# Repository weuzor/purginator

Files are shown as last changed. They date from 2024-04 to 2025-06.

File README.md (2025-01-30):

# The Purginator - a purge bucket for the Voron2

The purginator, extractor and depressor are modifications for Voron 2 Printers fitted with Voron Tap, umbilical Stealthburner with E3D Revo hotend (other hotends probably work as well), Filametrix Cutter Mod and Enraged Rabbit Carrot Feeder using sensorless homing and running Happy Hare.
In combination they enable multi material printing without purge tower.

## Purginator

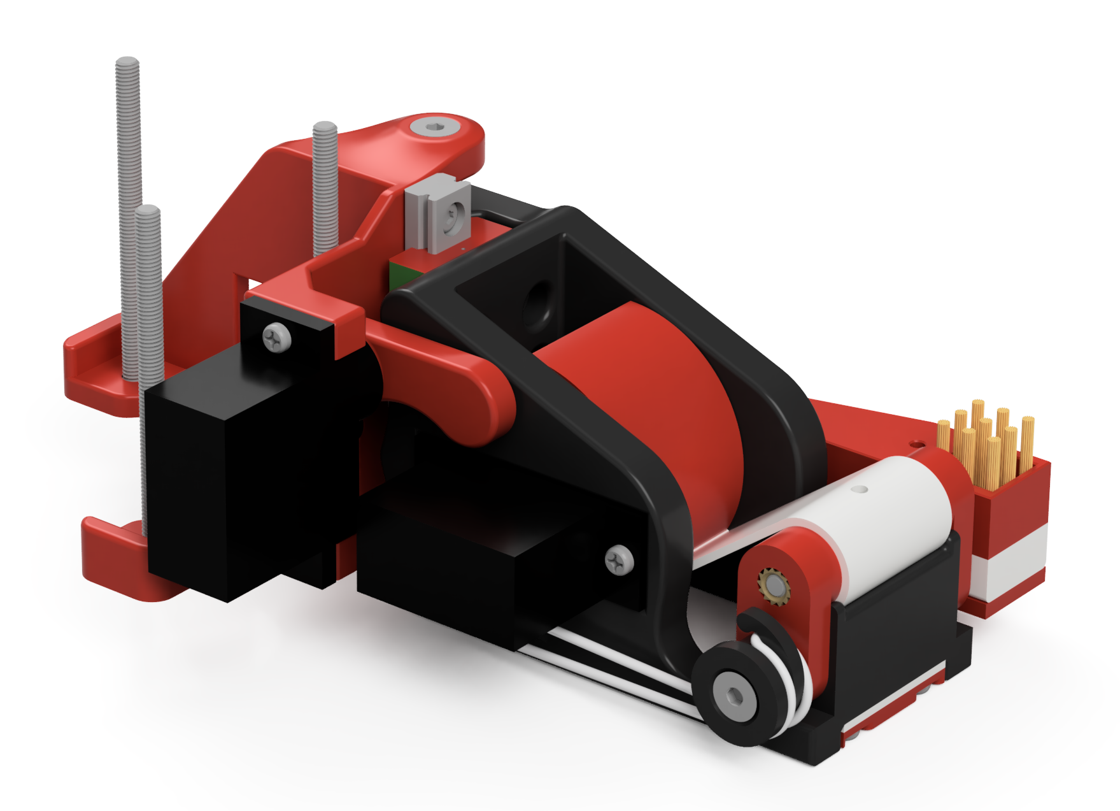
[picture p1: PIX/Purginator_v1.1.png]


([15 min Testprint showing toolchanges and after print nozzle treatment with the purginator](https://youtu.be/EkpkXMRFAnM)). 

## Extractor

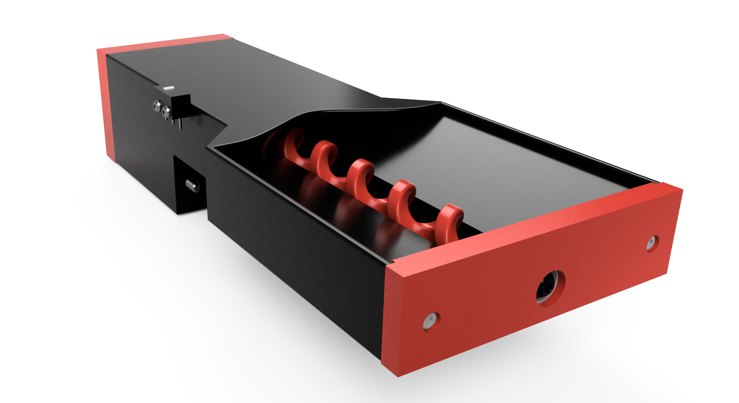
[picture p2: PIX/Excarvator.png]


The extractor is a collecting tray for the purged filament dropped by the purginator.
It has a built in screw conveyor which drags the purged material out of the printer through a small heat trap.
The screw conveyor is powered by a MG90S 360deg Servo.
Once outside the material can either be collected in a suitable container at the back of the printer or if the printer is placed at the rear of a table directly droped into a waste basket on the floor.
This modification requires a cutout in the backpanel. It also restricts z movement to 4 mm below print surface. 
For normal operation this is irrelevant, however if a Z-Homing or Quad Gantry Levelling is performed and the rear left gantry corner is lower than the others by more than 4 mm (e. g. after motors were off and the gantry was moved by whatever cause) the purginator mount would collide with the excarvator. 
To prevent this the extractor has mounting holes for a safety microswitch to trigger an emergency shutdown in this case.

## [Filametrix](https://github.com/sorted01/Filametrix) Depressor 
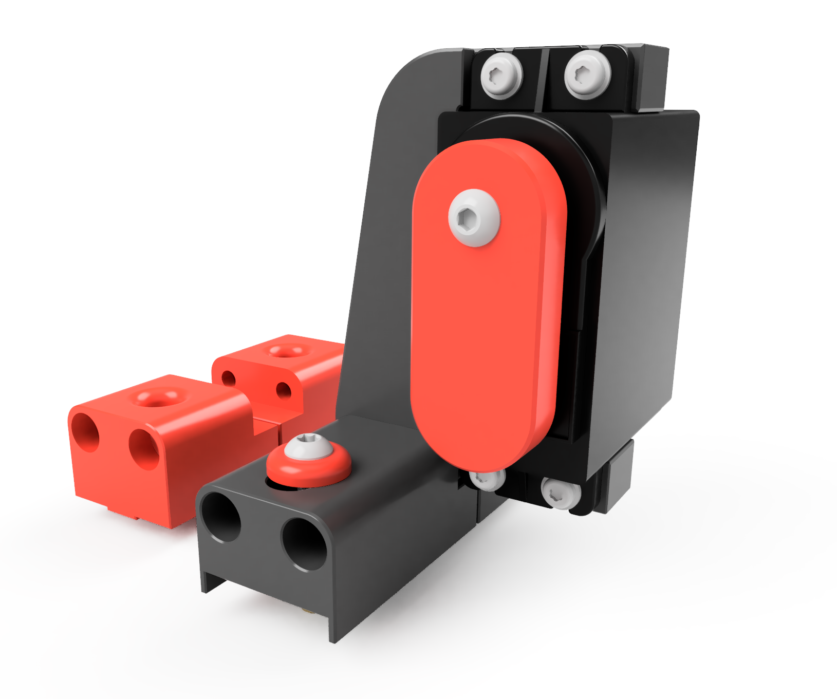
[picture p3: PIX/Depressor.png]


https://github.com/user-attachments/assets/b3596728-9525-4a37-93d0-bf73759ecd00

This mod places a strong enough MG996R Servo at a location where it does not interfere with the toolhead but can depress the filametrix cutter lever with its servo arm.
Thereby the toolhead can remain docked to the purginator during the cutting sequence which eliminates oozing.
Comes with two mounting options for gantries with backers or without.

As an alternative to the gantry mounted depressor this [bowden actuated filament cutter](https://github.com/weuzor/bowden_cutter) can also be used instead to cut any time anywhere :-)

hot1
ex2

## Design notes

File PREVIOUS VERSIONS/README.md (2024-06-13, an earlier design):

# Voron 2 Modifications for multi material printing with ERCF and Stealthburner with Filametrix Cutter
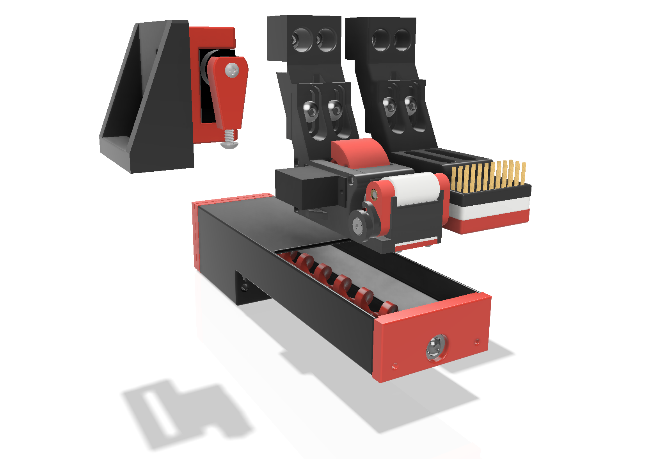
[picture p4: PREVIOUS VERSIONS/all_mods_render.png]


## The Purginator
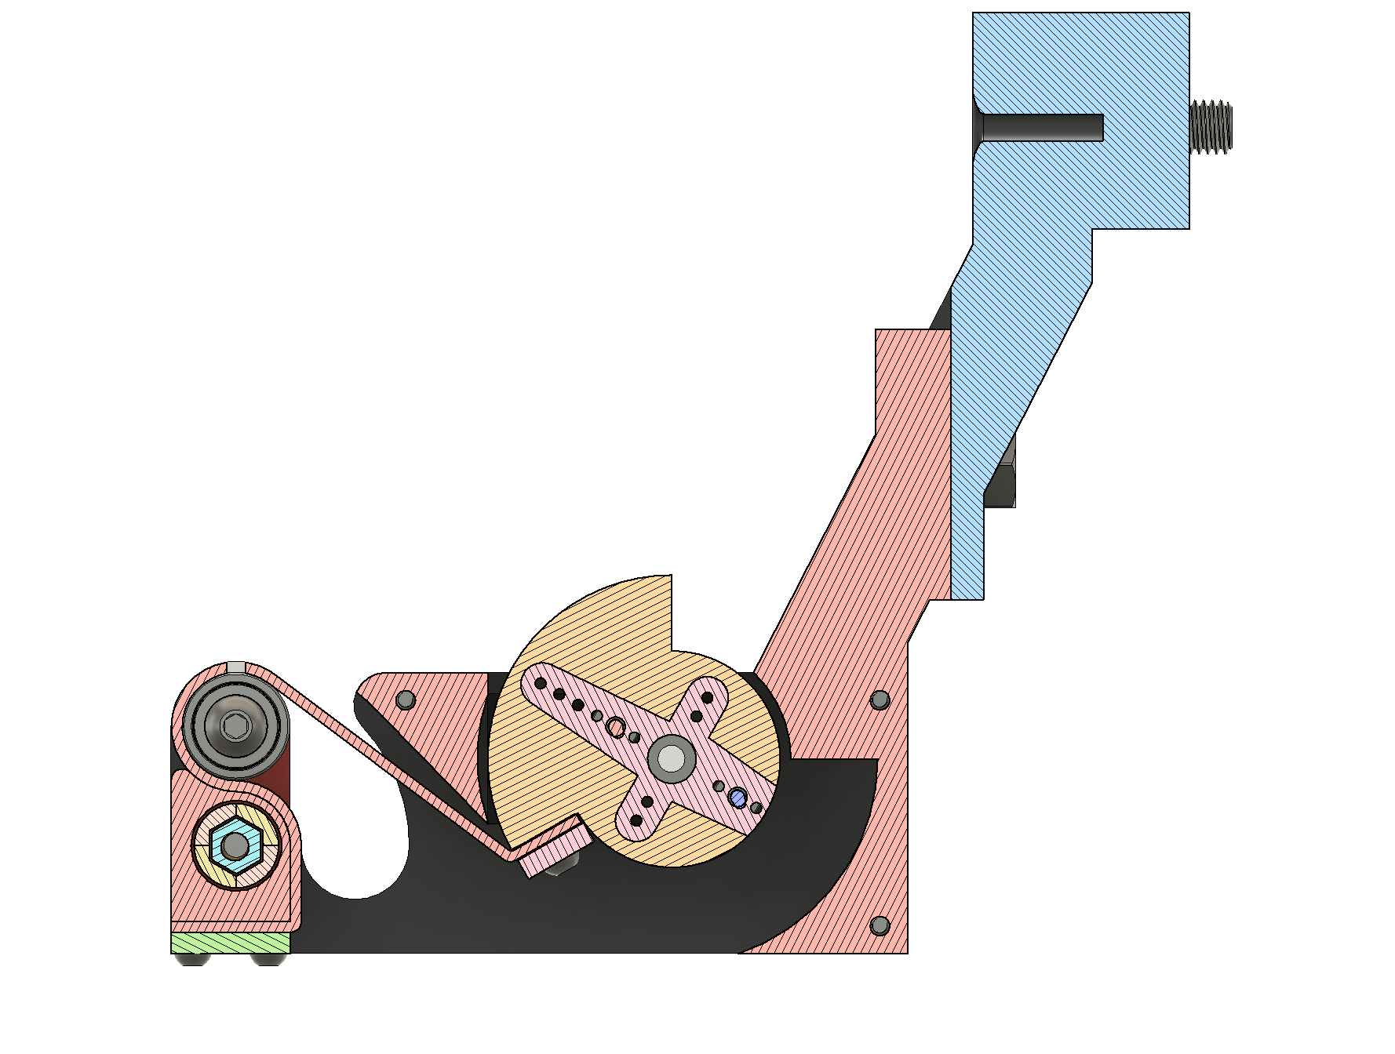
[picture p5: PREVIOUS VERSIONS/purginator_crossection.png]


The purginator is a gantry mounted mechanized purge bucket driven by a MG90S Servo.
In extended position a strip of silicone with a hole is bent into a loop like shape nestling the hole to the nozzle for purging. 
When retracting the silicone strip gets stretched out. This motion wipes the nozzle tip and drops the purged filament.
Installing a purginator enables multi material printing without purge/prime tower thus keeping the entire printbed available for model files. 
[Watch a proof of concept video of a short 3 colour testprint with the purginator, brushinator and gantry servo mount](https://youtu.be/IaCVgWm7dVc). 
It also provides a place to park the toolhead for warmup/cooldown where oozing is no problem.

## The Excarvator
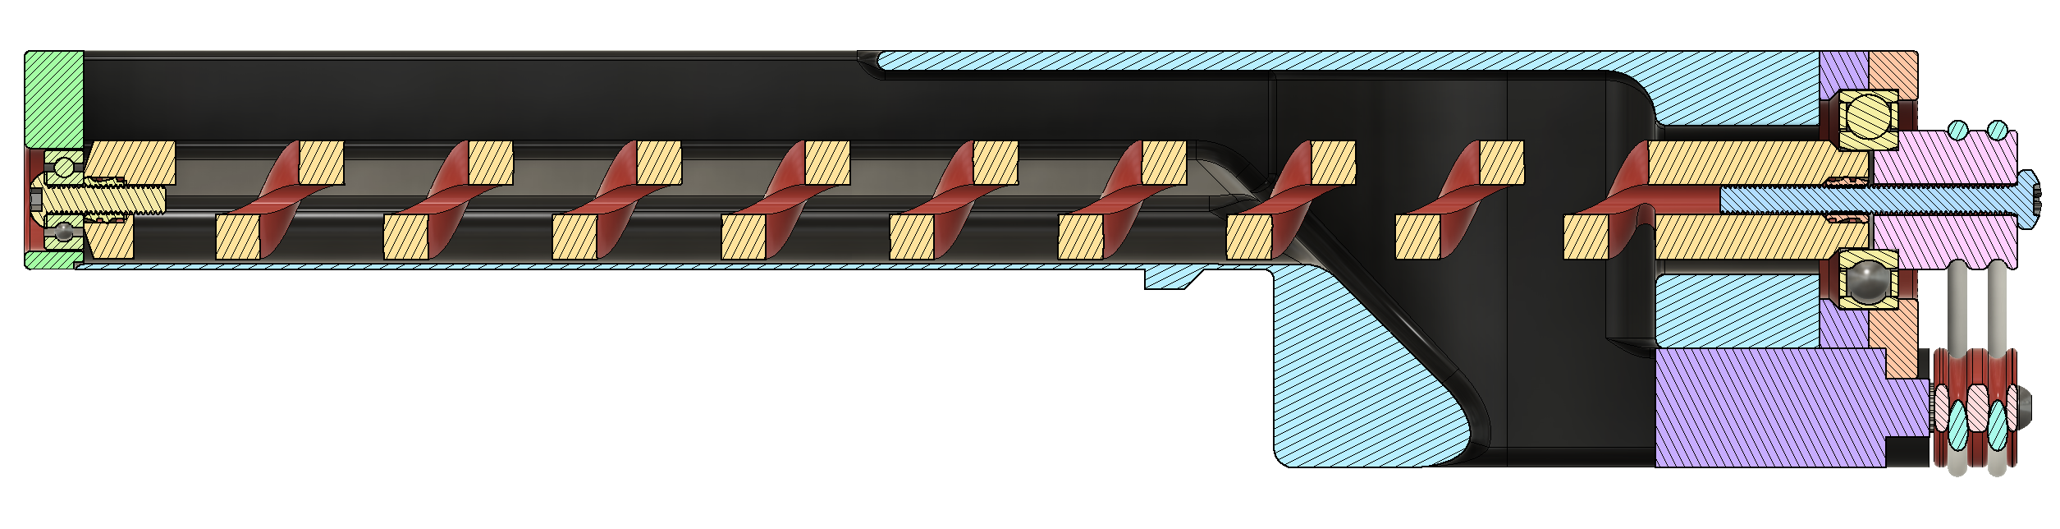
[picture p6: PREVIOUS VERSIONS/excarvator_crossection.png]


The excarvator is a collecting tray for the purged filament dropped by the purginator. It has a built in screw conveyor which drags the purged material out of the printer through a small heat trap.
The screw conveyor is powered by a MG90S 360deg Servo.
Once outside the material can either be collected in a suitable container at the back of the printer or if the printer is placed at the rear of a table directly droped into a waste basket on the floor.
This modification requires a cutout in the backpanel!

## The Brushinator
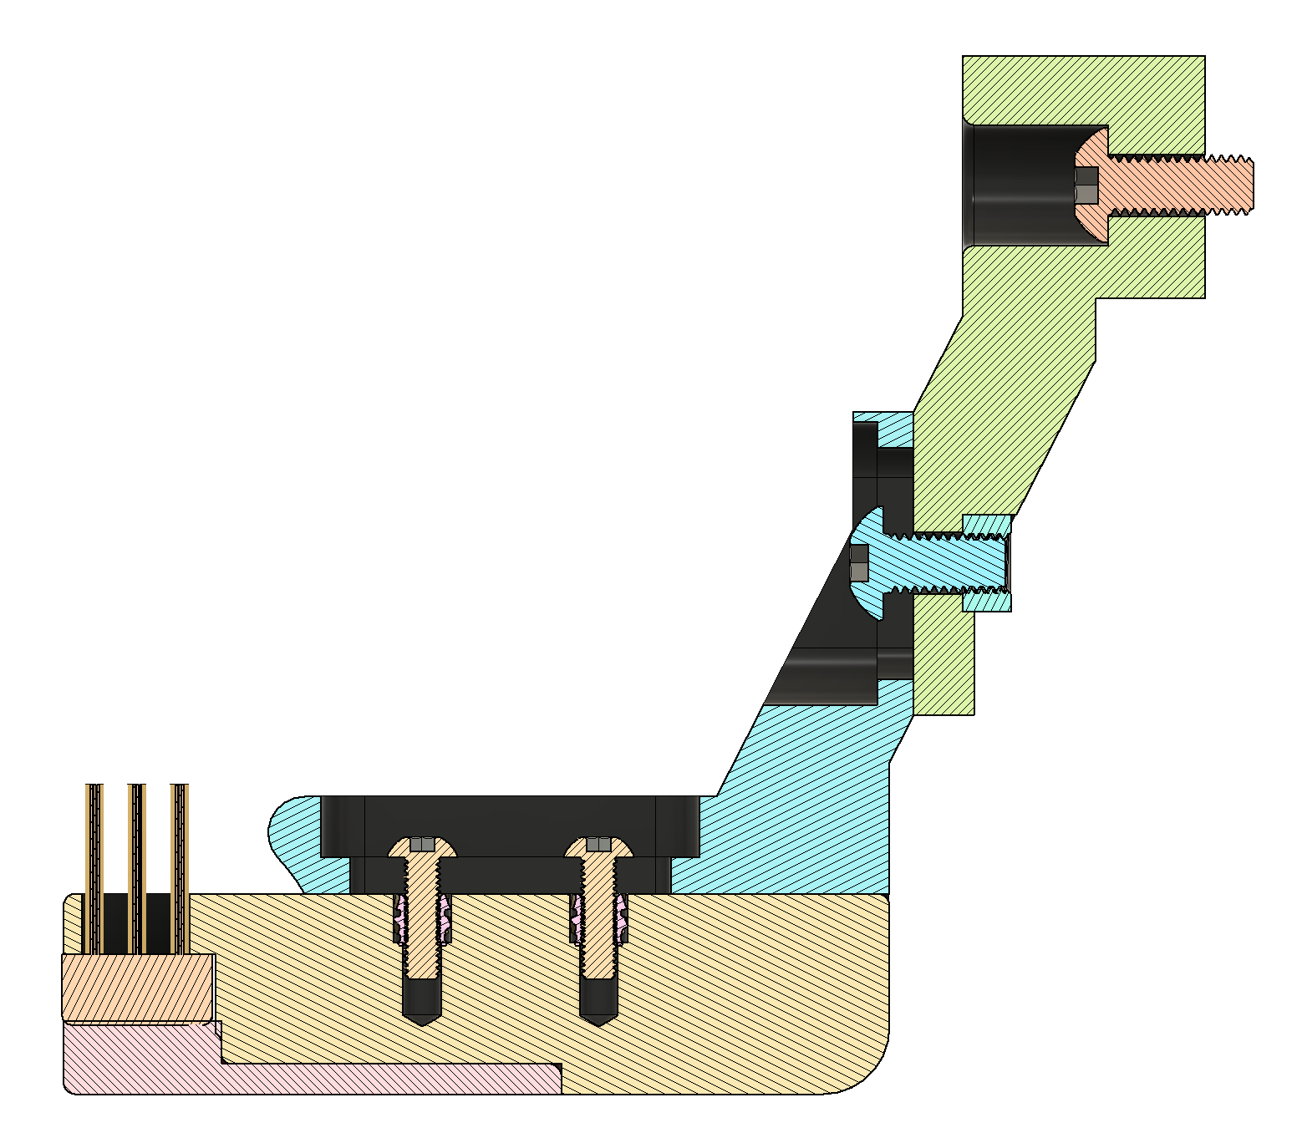
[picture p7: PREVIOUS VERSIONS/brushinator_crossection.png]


The brushinator is a cheap copy of [this gantry mounted nozzle cleaner](https://www.printables.com/de/model/269412-voron-v24-300-gantry-mounted-nozzle-cleaner) matching the purginator design.

## Gantry Servo Mount + Pin
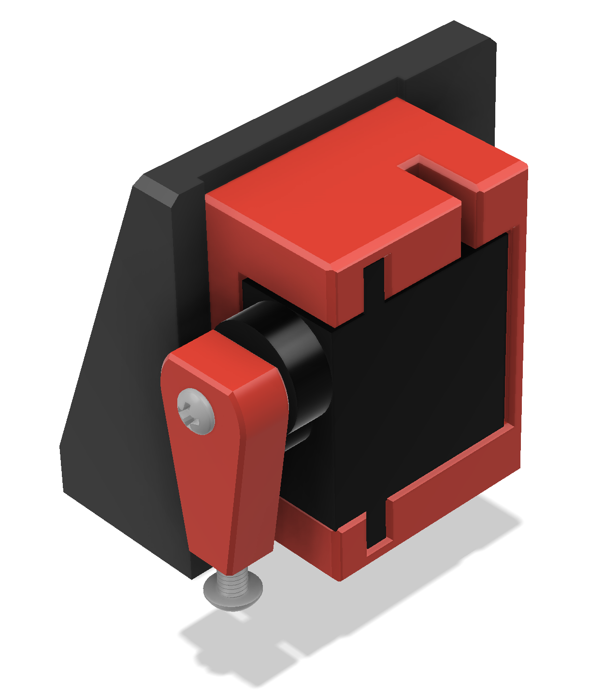
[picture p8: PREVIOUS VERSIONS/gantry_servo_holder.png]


After installing the Filametrix Cutting Mod I realized that the fixed pin interferes with the Stealthburner when moving around the top left corner of the printbed which is something I could not live with.
Since there is a config option for a retracting [Filametrix Cutting Mod](https://github.com/sorted01/Filametrix) pin in the [Happy Hare Software](https://github.com/moggieuk/Happy-Hare) I began my search for the appropriate STL files.
A few hours later I gave up and built my own. It is adjustable in all axes and fits the gantry with or without backers.

## Bill of Materials:

### Purginator 
* [1mm high temperature silicone sheet](https://www.amazon.de/gp/product/B08KFTPTG9/ref=ppx_yo_dt_b_asin_title_o04_s00?ie=UTF8&th=1)
* [1 ea silicone O-Ring 10x14x2mm](https://www.amazon.de/gp/product/B07NQD6KCJ/ref=ppx_yo_dt_b_asin_title_o03_s00?ie=UTF8&th=1)
* [1ea MG90s 180deg Servo](https://www.amazon.de/gp/product/B086V3VP72/ref=ppx_yo_dt_b_asin_title_o00_s00?ie=UTF8&th=1)
* [2ea Ballbearings 3x10x4mm](https://www.amazon.de/stücke-623-2RS-Kugellager-Doppel-Rillenkugellager/dp/B07CWLGNJ5/ref=sr_1_1_sspa?dib=eyJ2IjoiMSJ9.9woqqwQjTq-p6iPwrUffi2d2bsHJw6UycUsB92_u3q-Smt9jMfxYufze3yMLa8dVCcguvt3fg-eWgwVzRmbCx6OBDLn50Iqe8E2cVwwDzqe9K4E6B9IgL00jBknB56GO1ZkXVQhbH0jbnrGV-QxXVfFCnwxjZPuh-A0WkN2nheVrjfzndKp1NyEEW4B8PbHB0m_gXTPkrTWZJLG8WaGOHKBgCCyeGjlpAJjDO7ynSQw.av6AitDux3gb7yG6LLjvQHgYDzAzVkIL2xda3fSPe5c&dib_tag=se&keywords=Kugellager+3x10x4&qid=1710786944&sr=8-1-spons&sp_csd=d2lkZ2V0TmFtZT1zcF9hdGY&psc=1)
* 2ea brass heat insert 4mm
* 2ea M3x10 button head screw
* [1ea 20mm M3 brass standoff](https://www.amazon.de/AMZANDY-NEW-Abstandshalter-Abstandsbolzen-Motherboard-120/dp/B0825XY6VD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)
* 1ea M3x10 countersunk screw
* 1ea M3x20 countersunk screw
* 2ea M2x10 button head screw
* 4ea M2x5 button head screw
* 3ea 2x10 self tapping screw
* 2ea M5x10 button head screw
* 2ea M5 hex nut
* 2ea M5x12 screw
* 2ea M5 roll in T-nuts

### Brushinator 
* 1ea [Brush](https://www.amazon.de/Reinigung-Drahtbürste-Kunststoffgriffe-Edelstahl-Reinigungswerkzeug/dp/B0895GCSH7/ref=sxts_b2b_sx_reorder_acb_customer?content-id=amzn1.sym.f4e69c76-7f1e-4be9-a990-6de7d07aaf6a%3Aamzn1.sym.f4e69c76-7f1e-4be9-a990-6de7d07aaf6a&crid=20N7CF5QOWQE5&cv_ct_cx=messingbürste&dib=eyJ2IjoiMSJ9.z7TWS4HkcxDzHbvJIgCPzA.Y7QLxHE9fQSL7NgeJQ0xp0zurahyunnSiQJpj-z_JAI&dib_tag=se&keywords=messingbürste&pd_rd_i=B0895GCSH7&pd_rd_r=83d5e4a9-06be-4864-90a7-eb933d223a5d&pd_rd_w=HD1Tp&pd_rd_wg=Qrf1B&pf_rd_p=f4e69c76-7f1e-4be9-a990-6de7d07aaf6a&pf_rd_r=70E8QH3QH7KNRC2K66PZ&qid=1710793370&sbo=RZvfv%2F%2FHxDF%2BO5021pAnSA%3D%3D&sprefix=messingbürste%2Caps%2C100&sr=1-1-c8a51df4-6015-4603-b82a-8c2c24cf7e97&th=1)
* 4ea brass heat insert 4mm
* 4ea M3x10 button head screw
* 2ea M5x10 button head screw
* 2ea M5 hex nut
* 2ea M5x12 button head screw
* 2ea M5 roll in T-nuts

### Excarvator
* 1ea M3x30 button head screw
* [2 ea silicone O-Ring 10x14x2mm](https://www.amazon.de/gp/product/B07NQD6KCJ/ref=ppx_yo_dt_b_asin_title_o03_s00?ie=UTF8&th=1)
* 1ea MG90s 360deg Servo (Aliexpress)
* 2ea brass heat insert 4mm
* 1ea M3x10 button head screw
* 1ea ballbearing 3x10x4mm
* 1ea ballbearing 10x22x6mm
* 2ea 2x10 self tapping screw
* 2ea M2.5x16 button head screw
* 2ea M3x16 button head screw

### Gantry Servo Mount & Pin for Filametrix Filament Cutter.
* 1ea 15mm M3 brass standoff
* 1ea M3x16 button head screw
* 1ea MG90s 180deg Servo
* 1ea brass heat insert 4mm
* 1ea M3x10 button head screw

## Building Instructions
### Purginator
* With a ruler and a scalpel cut out a 82x20 mm strip of 1mm thick silicone sheet and punch 2.5 mm holes according to the template. This ist best done with [punch pliers](https://www.amazon.de/AmazonBasics-Leder-Lochzangen-Set-Drehlochzange-verschiedene-Aufweitwerkzeug/dp/B07W48YG15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) and the jig which can be found amongst the stl files.
* Mount the 4 armed servo horn that came with the MG90s servo to the retraction drum using the screws which were included as well and cut the protruding arm flush
* Insert a heat insert in each of the bearing levers
* Mount the ballbearings to the bearing levers
* Fix the 20mm brass standoff to one of the bearing levers using a M3x10 countersunk screw.
* Insert into the main body and the lid
* Mount the second bearing lever and the torque inducer using a M3x20 countersunk screw. Tighten so that the torque inducer does not slip.
* Stretch the silicone O-ring over the torque inducer and fix it to the hook on the main body.
* Mount the silicone strip to the retraction drum using the drum clamp and two M2x10 screws. Make sure the strip is perpendicular to the drum.
* Place the drum in the main body and run the silicone strip in a loop around the bearings.
* Slide the cover in place and secure with three 2x10mm tapping screws.
* Fix the silicone strip end to the housing bottom using the fwd clamp and 4 M2x5 screws. Make sure not to overtighten.
* Check for smooth action.
* Place the M5 hex nuts in the gantry mount (and maybe secure them with some glue)
* Mount the assembly to the gantry mount using two M5x10 button head screws
* The servo should be inserted in position ANGLE=180 and the purginator drum in fully retracted position.
* Mount to the left gantry corner flush to the aluminium extrusion.

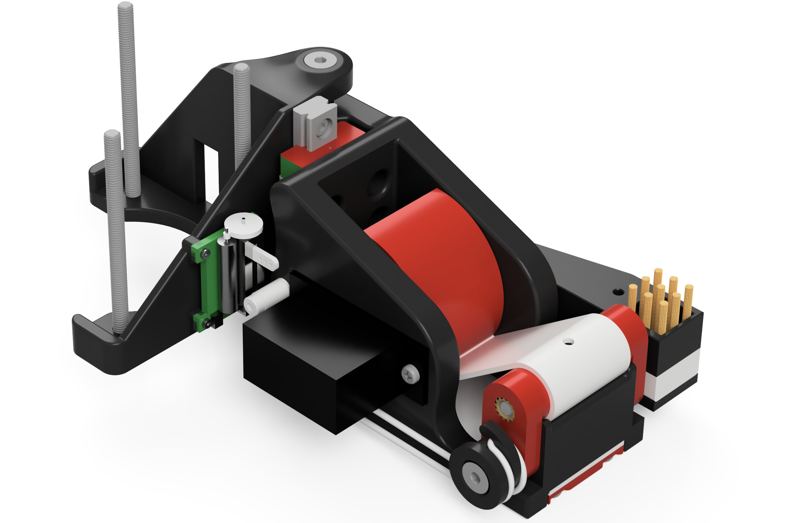
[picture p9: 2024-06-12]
PIX/Purginator_v1.0.png

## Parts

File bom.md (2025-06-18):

# BOM (unfinished work in progress)
## purginator
* 2 [MG90s 180deg servo](https://www.amazon.de/gp/product/B086V3VP72/ref=ppx_yo_dt_b_asin_title_o00_s00?ie=UTF8&th=1)
* 2 [Ballbearing 3x10x4mm](https://www.amazon.de/stücke-623-2RS-Kugellager-Doppel-Rillenkugellager/dp/B07CWLGNJ5/ref=sr_1_1_sspa?dib=eyJ2IjoiMSJ9.9woqqwQjTq-p6iPwrUffi2d2bsHJw6UycUsB92_u3q-Smt9jMfxYufze3yMLa8dVCcguvt3fg-eWgwVzRmbCx6OBDLn50Iqe8E2cVwwDzqe9K4E6B9IgL00jBknB56GO1ZkXVQhbH0jbnrGV-QxXVfFCnwxjZPuh-A0WkN2nheVrjfzndKp1NyEEW4B8PbHB0m_gXTPkrTWZJLG8WaGOHKBgCCyeGjlpAJjDO7ynSQw.av6AitDux3gb7yG6LLjvQHgYDzAzVkIL2xda3fSPe5c&dib_tag=se&keywords=Kugellager+3x10x4&qid=1710786944&sr=8-1-spons&sp_csd=d2lkZ2V0TmFtZT1zcF9hdGY&psc=1)
* 1 [LWL7B 40mm Mini Linear Rail](https://www.amazon.de/gp/product/B07N2T7YQX/ref=ppx_yo_dt_b_asin_image_o04_s00?ie=UTF8&psc=1)
* 1 [20mm female threaded M3 brass hex standoff](https://www.amazon.de/AMZANDY-NEW-Abstandshalter-Abstandsbolzen-Motherboard-120/dp/B0825XY6VD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)
* 1 [1mm high temperature silicone sheet](https://www.amazon.de/gp/product/B08KFTPTG9/ref=ppx_yo_dt_b_asin_title_o04_s00?ie=UTF8&th=1)
* 1 [silicone O-Ring 10x14x2mm](https://www.amazon.de/gp/product/B07NQD6KCJ/ref=ppx_yo_dt_b_asin_title_o03_s00?ie=UTF8&th=1)
* 1 [Brush](https://www.amazon.de/Reinigung-Drahtbürste-Kunststoffgriffe-Edelstahl-Reinigungswerkzeug/dp/B0895GCSH7/ref=sxts_b2b_sx_reorder_acb_customer?content-id=amzn1.sym.f4e69c76-7f1e-4be9-a990-6de7d07aaf6a%3Aamzn1.sym.f4e69c76-7f1e-4be9-a990-6de7d07aaf6a&crid=20N7CF5QOWQE5&cv_ct_cx=messingbürste&dib=eyJ2IjoiMSJ9.z7TWS4HkcxDzHbvJIgCPzA.Y7QLxHE9fQSL7NgeJQ0xp0zurahyunnSiQJpj-z_JAI&dib_tag=se&keywords=messingbürste&pd_rd_i=B0895GCSH7&pd_rd_r=83d5e4a9-06be-4864-90a7-eb933d223a5d&pd_rd_w=HD1Tp&pd_rd_wg=Qrf1B&pf_rd_p=f4e69c76-7f1e-4be9-a990-6de7d07aaf6a&pf_rd_r=70E8QH3QH7KNRC2K66PZ&qid=1710793370&sbo=RZvfv%2F%2FHxDF%2BO5021pAnSA%3D%3D&sprefix=messingbürste%2Caps%2C100&sr=1-1-c8a51df4-6015-4603-b82a-8c2c24cf7e97&th=1)
* 1 [7x12x0.5 compression spring](https://www.amazon.de/dp/B08SKBBG2T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)
* 3 [M3 x 45 countersunk screw](https://www.amazon.de/Senkschrauben-Innensechskant-Edelstahl-rostfrei-Senkkopfschraube/dp/B09BL34P6R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)
* 1 M3 x 40 countersunk screw
* 4 4mm M3 heat inserts
* 8 M2 x 6 tapping screws
* 4 M2 x 16 Tapping screw
* 2 M3 x 6 screw

## extractor
* 2 [Silicone O-Ring 10x14x2mm](https://www.amazon.de/gp/product/B07NQD6KCJ/ref=ppx_yo_dt_b_asin_title_o03_s00?ie=UTF8&th=1)
* 1 MG90s 360deg Servo (Aliexpress) or [modified](https://www.youtube.com/watch?v=JhHSXCLsN4k) MG90s 180deg servo
* 1 [Ballbearing 3x10x4mm](https://www.amazon.de/stücke-623-2RS-Kugellager-Doppel-Rillenkugellager/dp/B07CWLGNJ5/ref=sr_1_1_sspa?dib=eyJ2IjoiMSJ9.9woqqwQjTq-p6iPwrUffi2d2bsHJw6UycUsB92_u3q-Smt9jMfxYufze3yMLa8dVCcguvt3fg-eWgwVzRmbCx6OBDLn50Iqe8E2cVwwDzqe9K4E6B9IgL00jBknB56GO1ZkXVQhbH0jbnrGV-QxXVfFCnwxjZPuh-A0WkN2nheVrjfzndKp1NyEEW4B8PbHB0m_gXTPkrTWZJLG8WaGOHKBgCCyeGjlpAJjDO7ynSQw.av6AitDux3gb7yG6LLjvQHgYDzAzVkIL2xda3fSPe5c&dib_tag=se&keywords=Kugellager+3x10x4&qid=1710786944&sr=8-1-spons&sp_csd=d2lkZ2V0TmFtZT1zcF9hdGY&psc=1)
* 1 [ballbearing 10x22x6mm](https://www.amazon.de/sourcing-map-Rillenkugellager-geschirmt-Kohlenstoffstahl/dp/B0822KX26F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)
* 2 4mm M3 heat inserts

## depressor

* 1 [MG996R Servo (180 deg)](https://www.amazon.de/YUNIQUE-DEUTSCHLAND-Digitale-Lenkservo-Helikopter/dp/B01I3Y3F88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)
* 2 [10mm male/female threaded M3 brass hex standoff](https://www.amazon.de/AMZANDY-NEW-Abstandshalter-Abstandsbolzen-Motherboard-120/dp/B0825XY6VD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) (only needed for backers version)
* 2 M3x40 screws
* 2 M3x12 screws

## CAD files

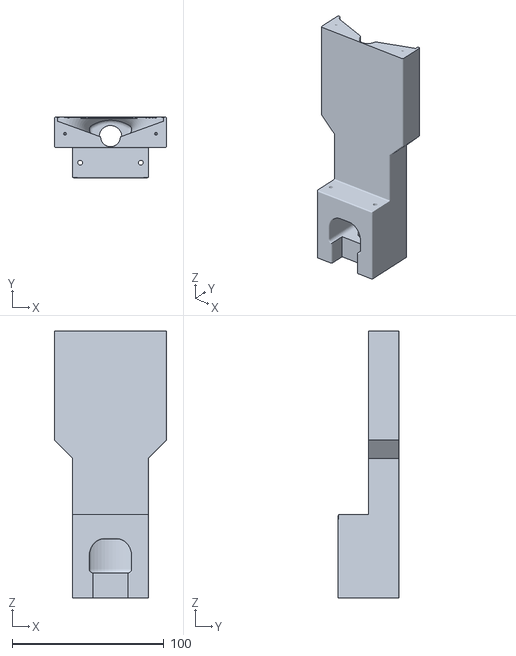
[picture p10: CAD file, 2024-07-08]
STL/EXTRACTOR/MAIN BODY.stl
74.0 x 40.0 x 176.0

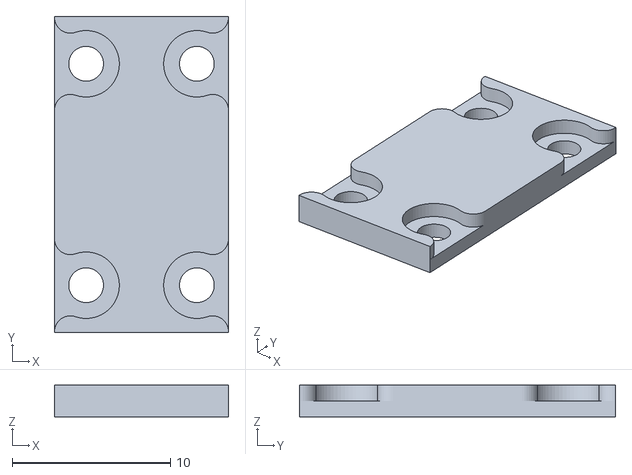
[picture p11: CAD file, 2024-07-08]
STL/PURGINATOR/Main Body Clamp.stl
11.0 x 20.0 x 2.00

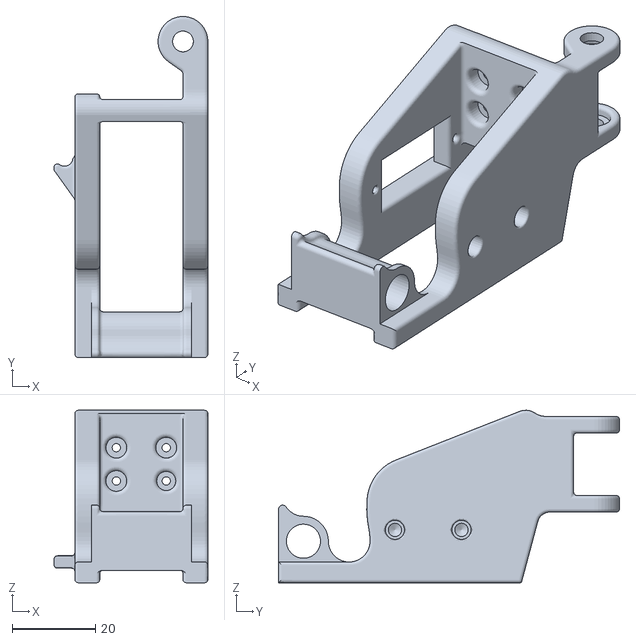
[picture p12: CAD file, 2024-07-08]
STL/PURGINATOR/Main Body.stl
37.0 x 82.0 x 41.5

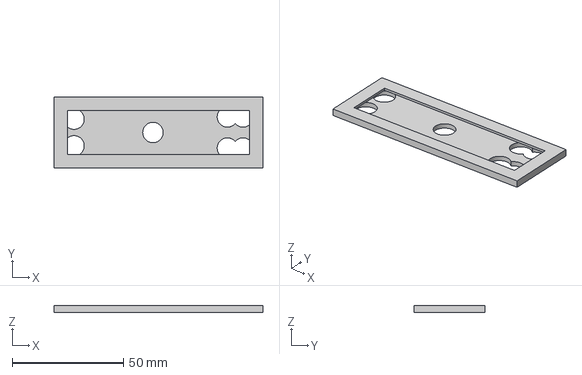
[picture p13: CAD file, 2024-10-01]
CAD/Hole_punching_jig.step
94.0 x 32.0 x 3.00 mm

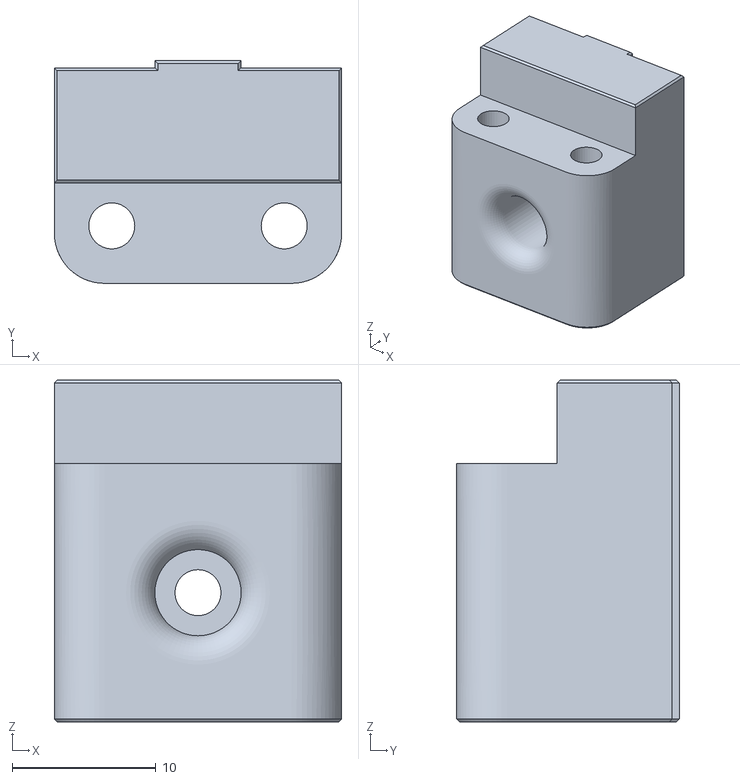
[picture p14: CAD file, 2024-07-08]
STL/DEPRESSOR/Mounting Base FRONT No Backers.stl
20.0 x 15.5 x 23.8

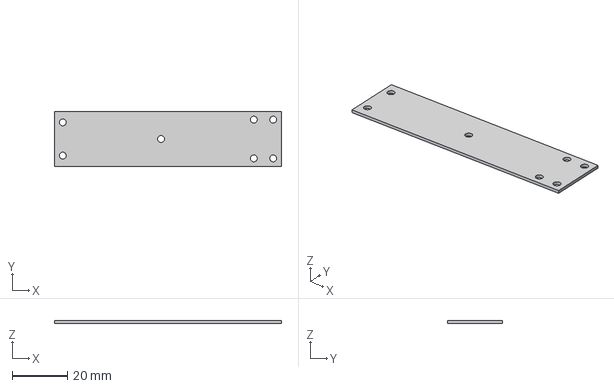
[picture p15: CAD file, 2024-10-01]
CAD/Silicone_strip_template.step
82.0 x 20.0 x 1.00 mm

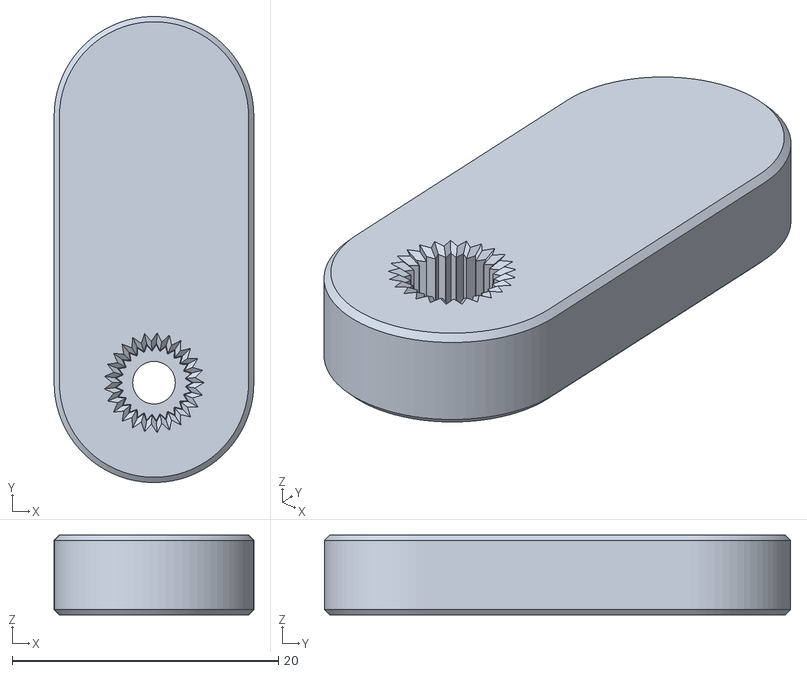
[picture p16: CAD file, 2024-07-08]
STL/DEPRESSOR/Servo Arm.stl
15.0 x 35.0 x 6.00

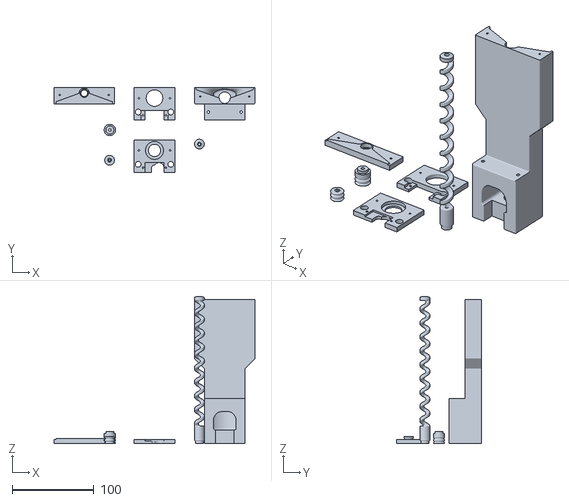
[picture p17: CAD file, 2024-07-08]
STL/EXTRACTOR/All Parts.stl
246.0 x 104.0 x 180.0

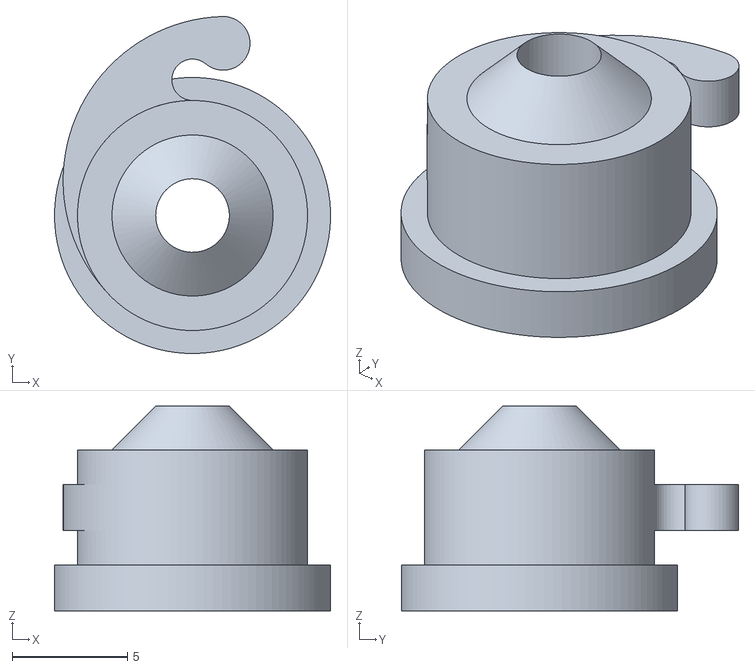
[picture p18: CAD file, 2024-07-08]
STL/PURGINATOR/Torque Inducer.stl
12.0 x 14.6 x 8.90

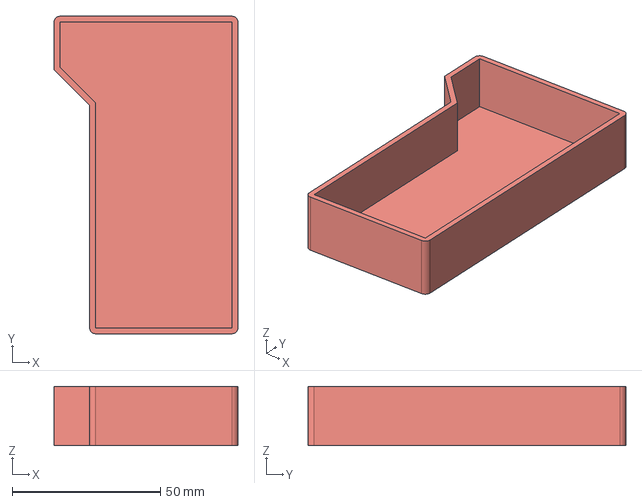
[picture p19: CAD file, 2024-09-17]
CAD/Brush_Tray_350.step
62.0 x 107.0 x 20.0 mm

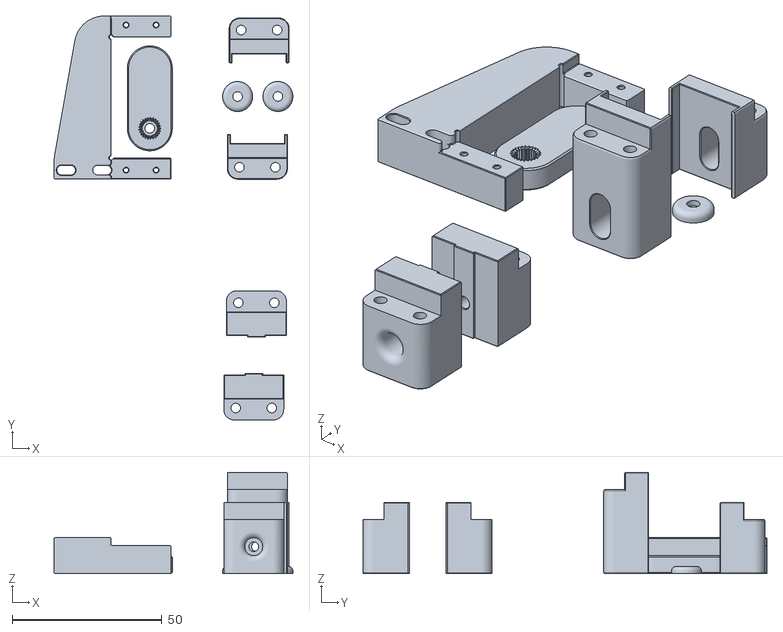
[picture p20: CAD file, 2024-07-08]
STL/DEPRESSOR/All Parts.stl
79.6 x 134.7 x 33.8

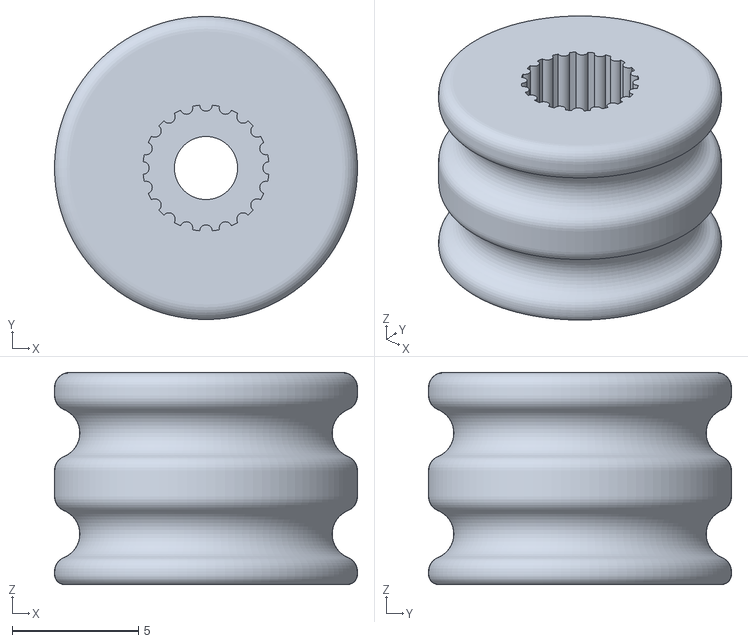
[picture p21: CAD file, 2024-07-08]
STL/EXTRACTOR/Servo_Pulley.stl
12.0 x 12.0 x 8.40

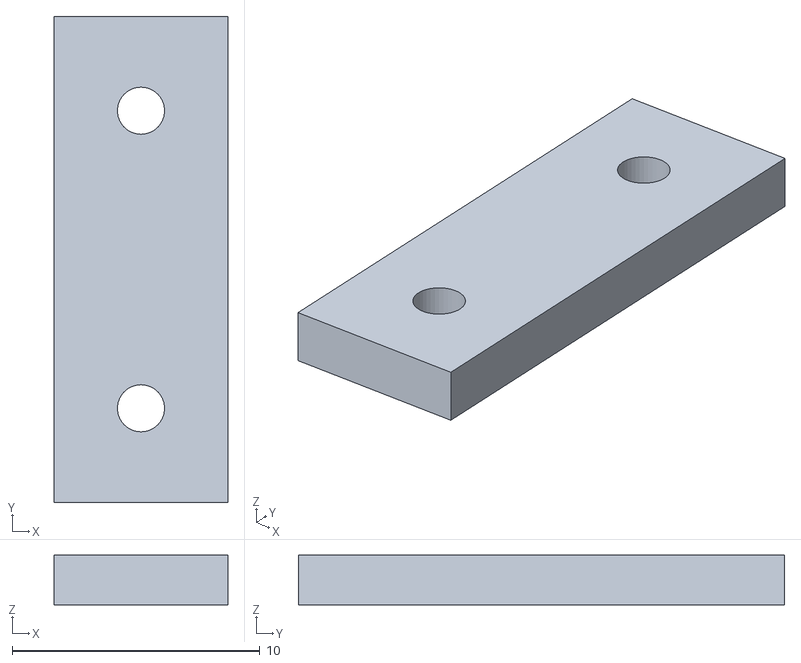
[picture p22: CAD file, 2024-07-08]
STL/PURGINATOR/Drum Clamp.stl.stl
7.00 x 19.6 x 2.00

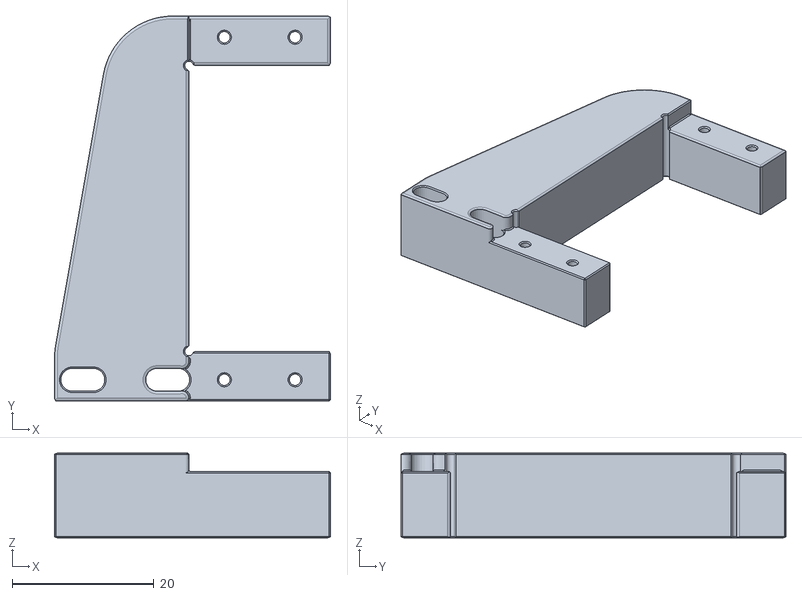
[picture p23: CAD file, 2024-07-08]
STL/DEPRESSOR/Servo Bracket.stl
39.0 x 54.4 x 12.0

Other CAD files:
STL/PURGINATOR/Brush Clamp.stl
STL/DEPRESSOR/Mounting Base REAR No Backers.stl
STL/EXTRACTOR/REAR OUTER ENDPIECE.stl
STL/PURGINATOR/Brush Holder.stl.stl
PREVIOUS VERSIONS/BRUSHINATOR/STL/brush_holder.stl
PREVIOUS VERSIONS/BRUSHINATOR/STL/brush_lock.stl
PREVIOUS VERSIONS/BRUSHINATOR/STL/elbow.stl
PREVIOUS VERSIONS/BRUSHINATOR/STL/gantry_mount.stl
PREVIOUS VERSIONS/EXCARVATOR/STL/Collecting_Tray.stl
PREVIOUS VERSIONS/EXCARVATOR/STL/Fwd_Endpiece.stl
PREVIOUS VERSIONS/EXCARVATOR/STL/Rear_Endpiece_Inner.stl
PREVIOUS VERSIONS/EXCARVATOR/STL/Rear_Endpiece_Outer.stl
PREVIOUS VERSIONS/EXCARVATOR/STL/Screw_Conveyor.stl
PREVIOUS VERSIONS/EXCARVATOR/STL/Screw_Conyeyor_Pulley.stl
PREVIOUS VERSIONS/EXCARVATOR/STL/Servo_Pulley.stl
PREVIOUS VERSIONS/Gantry Servo Mount and Pin/STL/mounting_bracket.stl
PREVIOUS VERSIONS/Gantry Servo Mount and Pin/STL/mounting_bracket_backer_compat.stl
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

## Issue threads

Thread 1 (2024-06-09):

missing Klipper macro file

JunyuMu, 2024-06-09:
I'm building Purginator 2 + Excarvator 2 and I noticed that there is no marco.cfg provided.

weuzor, 2024-06-17:
not quite ready yet.

Closed 2024-06-24.

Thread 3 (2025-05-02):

Servo for depressor not exactly specified

toscdesign, 2025-05-02:
Hi,
You didn't specify exactly that a 180° servo must be used. Therefore, I bought a 360° servo, which doesn't work with Klipper. You should add that in the BOM.

weuzor, 2025-06-18:
Hi, for the depressor  a MG996R should be used. i did not know there were 360 deg servos of that servo.

Closed 2025-06-18.

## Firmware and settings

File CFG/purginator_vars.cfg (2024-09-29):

;██████╗ ██╗   ██╗██████╗  ██████╗ ██╗███╗   ██╗ █████╗ ████████╗ ██████╗ ██████╗        ██╗   ██╗ █████╗ ██████╗ ███████╗    ██████╗ ██████╗ ███████╗
;██╔══██╗██║   ██║██╔══██╗██╔════╝ ██║████╗  ██║██╔══██╗╚══██╔══╝██╔═══██╗██╔══██╗       ██║   ██║██╔══██╗██╔══██╗██╔════╝   ██╔════╝██╔════╝ ██╔════╝
;██████╔╝██║   ██║██████╔╝██║  ███╗██║██╔██╗ ██║███████║   ██║   ██║   ██║██████╔╝       ██║   ██║███████║██████╔╝███████╗   ██║     ██║  ███╗█████╗  
;██╔═══╝ ██║   ██║██╔══██╗██║   ██║██║██║╚██╗██║██╔══██║   ██║   ██║   ██║██╔══██╗       ╚██╗ ██╔╝██╔══██║██╔══██╗╚════██║   ██║     ██║   ██║██╔══╝  
;██║     ╚██████╔╝██║  ██║╚██████╔╝██║██║ ╚████║██║  ██║   ██║   ╚██████╔╝██║  ██║███████╗╚████╔╝ ██║  ██║██║  ██║███████║██╗╚██████╗╚██████╔╝██║     
;╚═╝      ╚═════╝ ╚═╝  ╚═╝ ╚═════╝ ╚═╝╚═╝  ╚═══╝╚═╝  ╚═╝   ╚═╝    ╚═════╝ ╚═╝  ╚═╝╚══════╝ ╚═══╝  ╚═╝  ╚═╝╚═╝  ╚═╝╚══════╝╚═╝ ╚═════╝ ╚═════╝ ╚═╝     
;
; Version 1.3 2024-09-20
;
; 
;
;     _ _                           _      _    _        
;  __| (_)__ ___ _ _  __ ____ _ _ _(_)__ _| |__| |___ ___
; (_-< | / _/ -_) '_| \ V / _` | '_| / _` | '_ \ / -_|_-<
; /__/_|_\__\___|_|    \_/\__,_|_| |_\__,_|_.__/_\___/__/
;                                                        
; The following line should be put in the (orca) slicer start g-code to store necessary slicer information used for
; automatic reduction of the purged volume by the prime tower prime volume if selected in the slicer
; as well as for nozzle z positioning after the initial toolchange.
; 
; _PURGINATOR_SLICER_VARS PT=[enable_prime_tower] PV=[prime_volume] PH=[initial_layer_print_height]
;
; If this is not possible for any reasons the default values will be used.
; 

[gcode_macro _PURGINATOR_SLICER_VARS]
description: Store slicer parameters for use in purge volume calculation
description: Put following line in the machine start g-code of the slicer:
description: _PURGINATOR_SLICER_VARS PT=[enable_prime_tower] PV=[prime_volume] PH=[initial_layer_print_height]
variable_enable_prime_tower:     False   # enable/disable purge volume reduction by prime tower volume
variable_prime_volume:               0   # prime tower prime volume
variable_initial_layer_print_height: 0.2 # needed for z placement of the toolhead where the print starts.
gcode:
    {% set enable_prime_tower = params.PT | default ( 0 ) | int == 1 %}
    {% set prime_volume = params.PV | default (0) | float %}
    {% set initial_layer_print_height = params.PH | default (initial_layer_print_height) |float %}
    RESPOND TYPE=command MSG="enable_prime_tower         : "{enable_prime_tower}
    RESPOND TYPE=command MSG="prime_volume               : "{prime_volume}
    RESPOND TYPE=command MSG="initial_layer_print_height : "{initial_layer_print_height}
    SET_GCODE_VARIABLE MACRO=_PURGINATOR_SLICER_VARS VARIABLE=enable_prime_tower VALUE={ enable_prime_tower }
    SET_GCODE_VARIABLE MACRO=_PURGINATOR_SLICER_VARS VARIABLE=prime_volume VALUE={ prime_volume }
    SET_GCODE_VARIABLE MACRO=_PURGINATOR_SLICER_VARS VARIABLE=initial_layer_print_height VALUE={ initial_layer_print_height }
    



[gcode_macro _PURGINATOR_VARS]

;  _                   _                                          _ _   _                                   _       _ _                          _                 
; | |                 | |                                        (_) | (_)                                 | |     | (_)                        (_)                
; | |__   __ _ _ __ __| |_      ____ _ _ __ ___   _ __   ___  ___ _| |_ _  ___  _ __  ___    __ _ _ __   __| |   __| |_ _ __ ___   ___ _ __  ___ _  ___  _ __  ___ 
; | '_ \ / _` | '__/ _` \ \ /\ / / _` | '__/ _ \ | '_ \ / _ \/ __| | __| |/ _ \| '_ \/ __|  / _` | '_ \ / _` |  / _` | | '_ ` _ \ / _ \ '_ \/ __| |/ _ \| '_ \/ __|
; | | | | (_| | | | (_| |\ V  V / (_| | | |  __/ | |_) | (_) \__ \ | |_| | (_) | | | \__ \ | (_| | | | | (_| | | (_| | | | | | | |  __/ | | \__ \ | (_) | | | \__ \
; |_| |_|\__,_|_|  \__,_| \_/\_/ \__,_|_|  \___| | .__/ \___/|___/_|\__|_|\___/|_| |_|___/  \__,_|_| |_|\__,_|  \__,_|_|_| |_| |_|\___|_| |_|___/_|\___/|_| |_|___/
;                                                | |                                                                                                               
;                                                |_|                                                                                                               

# Purge Position
variable_purge_pos_x:                                2.50    # X coordinate of the purge hole
variable_purge_pos_y:                              357.00    # Y coordinate of the purge hole

# Brush position
variable_brush_start:                               18.8     # X coordinate of lh bristles edge
variable_brush_end:                                 33.8     # X coordinate of rh bristles edge
variable_brush_front:                              352.0     # Y coordinate of the bristles front edge

# Z Homing Position
variable_z_homing_pos_x:                           175.00    # X coordinate of Z homing position
variable_z_homing_pos_y:                           175.00    # Y coordinate of Z homing position
variable_z_height_after_homing:                     20.00    # Z height after homing ( match with variable_minimum_purge_height )

# Away Position
variable_away_x:                                   350.00    # X coordinate of the away position
variable_away_y:                                   355.00    # Y coordinate of the away position
variable_away_z:                                   150.00    # Y coordinate of the away position

;                                             _ _   _                                   _                           _     
;                                            (_) | (_)                                 | |                         | |    
;  ___  ___ _ ____   _____    _ __   ___  ___ _| |_ _  ___  _ __  ___    __ _ _ __   __| |  ___ _ __   ___  ___  __| |___ 
; / __|/ _ \ '__\ \ / / _ \  | '_ \ / _ \/ __| | __| |/ _ \| '_ \/ __|  / _` | '_ \ / _` | / __| '_ \ / _ \/ _ \/ _` / __|
; \__ \  __/ |   \ V / (_) | | |_) | (_) \__ \ | |_| | (_) | | | \__ \ | (_| | | | | (_| | \__ \ |_) |  __/  __/ (_| \__ \
; |___/\___|_|    \_/ \___/  | .__/ \___/|___/_|\__|_|\___/|_| |_|___/  \__,_|_| |_|\__,_| |___/ .__/ \___|\___|\__,_|___/
;                            | |                                                               | |                        
;                            |_|                                                               |_|                        


# Retractor Servo positions and speed
variable_retractor_servo_angle_deployed:            10       # Servo angle purginator deployed (roller levers vertical) 
variable_retractor_servo_angle_retracted:           60       # Servo angle purginator retracted (roller levers about 15-20 deg from vertical) 
variable_retractor_servo_angle_eject:              180       # Servo angle at which the purginator in eject position (roller levers horizontal) 
variable_retractor_servo_speed:                    300       # Full servo stroke time (0-180) in ms

# Elevator Servo positions and speed
variable_elevator_servo_angle_up:                    0       # Elevator servo up angle (elevator servo upmost position)
variable_elevator_servo_angle_down:                110       # Elevator servo down angle (elevator servo pushing the purginator down so that nozzle tip is level with silicone)
variable_elevator_servo_speed:                     110       # Full servo stroke time (0-180) in ms

# Depressor Servo positions and speed
variable_depressor_servo_angle_deployed:            75       # Servo angle at which the depressor pushes the cutter lever far enough to cut the filament reliably 
variable_depressor_servo_angle_retracted:           10       # Servo angle at which the depressor is vertically pointing downwards and does not interfere with the toolhead
variable_depressor_servo_speed:                    800       # Full servo stroke time (0-180) in ms
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

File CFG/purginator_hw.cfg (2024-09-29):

;██████╗ ██╗   ██╗██████╗  ██████╗ ██╗███╗   ██╗ █████╗ ████████╗ ██████╗ ██████╗         ██╗  ██╗██╗    ██╗    ██████╗███████╗ ██████╗ 
;██╔══██╗██║   ██║██╔══██╗██╔════╝ ██║████╗  ██║██╔══██╗╚══██╔══╝██╔═══██╗██╔══██╗        ██║  ██║██║    ██║   ██╔════╝██╔════╝██╔════╝ 
;██████╔╝██║   ██║██████╔╝██║  ███╗██║██╔██╗ ██║███████║   ██║   ██║   ██║██████╔╝        ███████║██║ █╗ ██║   ██║     █████╗  ██║  ███╗
;██╔═══╝ ██║   ██║██╔══██╗██║   ██║██║██║╚██╗██║██╔══██║   ██║   ██║   ██║██╔══██╗        ██╔══██║██║███╗██║   ██║     ██╔══╝  ██║   ██║
;██║     ╚██████╔╝██║  ██║╚██████╔╝██║██║ ╚████║██║  ██║   ██║   ╚██████╔╝██║  ██║███████╗██║  ██║╚███╔███╔╝██╗╚██████╗██║     ╚██████╔╝
;╚═╝      ╚═════╝ ╚═╝  ╚═╝ ╚═════╝ ╚═╝╚═╝  ╚═══╝╚═╝  ╚═╝   ╚═╝    ╚═════╝ ╚═╝  ╚═╝╚══════╝╚═╝  ╚═╝ ╚══╝╚══╝ ╚═╝ ╚═════╝╚═╝      ╚═════╝ 
;
; Version 1.1 2024-09-24                                                                                                                        
; 

# Retractor MG90s 180deg Servo (deploy/retract the purginator)
[servo retractor]
pin: PB6                       
maximum_servo_angle: 180
minimum_pulse_width:   0.0005
maximum_pulse_width:   0.0025
initial_angle:        35  # servo at deployed position

# Elevator MG90s 180deg Servo (for vertical movement of the purginator)
[servo elevator]
pin: PB7                    
maximum_servo_angle: 180
minimum_pulse_width:   0.0005
maximum_pulse_width:   0.0025
initial_angle:         90  # servo in up position 

# Depressor MG996R Servo (cut filament with the Filametrix cutter)
[servo depressor]
pin: PG12                  
maximum_servo_angle: 180
minimum_pulse_width:   0.0005
maximum_pulse_width:   0.0025
initial_angle:        10  # depressor lever pointing vertically  downwards

# Extractor MG90s 360deg Servo (extract waste)
[servo extractor]
pin: PG13               
maximum_servo_angle: 180
minimum_pulse_width:   0.0005
maximum_pulse_width:   0.0025
initial_angle:        90  # neutral position

# Collision Prevention Safety Switch 
[gcode_button savior]
pin: ^!PG14   
press_gcode: 
  {action_emergency_stop("Collision prevention switch triggered. Manually lift rear left gantry corner a few millimeters before restart!")}

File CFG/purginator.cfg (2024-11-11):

;██████╗ ██╗   ██╗██████╗  ██████╗ ██╗███╗   ██╗ █████╗ ████████╗ ██████╗ ██████╗     ██████╗███████╗ ██████╗ 
;██╔══██╗██║   ██║██╔══██╗██╔════╝ ██║████╗  ██║██╔══██╗╚══██╔══╝██╔═══██╗██╔══██╗   ██╔════╝██╔════╝██╔════╝ 
;██████╔╝██║   ██║██████╔╝██║  ███╗██║██╔██╗ ██║███████║   ██║   ██║   ██║██████╔╝   ██║     █████╗  ██║  ███╗
;██╔═══╝ ██║   ██║██╔══██╗██║   ██║██║██║╚██╗██║██╔══██║   ██║   ██║   ██║██╔══██╗   ██║     ██╔══╝  ██║   ██║
;██║     ╚██████╔╝██║  ██║╚██████╔╝██║██║ ╚████║██║  ██║   ██║   ╚██████╔╝██║  ██║██╗╚██████╗██║     ╚██████╔╝
;╚═╝      ╚═════╝ ╚═╝  ╚═╝ ╚═════╝ ╚═╝╚═╝  ╚═══╝╚═╝  ╚═╝   ╚═╝    ╚═════╝ ╚═╝  ╚═╝╚═╝ ╚═════╝╚═╝      ╚═════╝ 
;
; Version 1.9 2024-11-11
;
; This file contains all macros necessary to make use of the Purginator mod (github.com/weuzor/purginator)
; Bear in mind that these macros were written by a person with only rudimentary knowledge in this area and are
; mostly the product of peeking into the happy hare macros by moggieuk and the blobifier.cfg by Dendrowen, 
; googeling and a lot of tries and even more errors, so general caution is advised if you plan to use them.


## Include Variables and Hardware Config 
[include purginator_vars.cfg]
[include purginator_hw.cfg]



;   _____ ___   ___              ____   _____ _        _____       _                       _   _             
;  / ____|__ \ / _ \    ___     / __ \ / ____| |      |_   _|     | |                     | | (_)            
; | |  __   ) | (_) |  ( _ )   | |  | | |  __| |        | |  _ __ | |_ ___  __ _ _ __ __ _| |_ _  ___  _ __  
; | | |_ | / / > _ <   / _ \/\ | |  | | | |_ | |        | | | '_ \| __/ _ \/ _` | '__/ _` | __| |/ _ \| '_ \ 
; | |__| |/ /_| (_) | | (_>  < | |__| | |__| | |____   _| |_| | | | ||  __/ (_| | | | (_| | |_| | (_) | | | |
;  \_____|____|\___/   \___/\/  \___\_\\_____|______| |_____|_| |_|\__\___|\__, |_|  \__,_|\__|_|\___/|_| |_|
;                                                                           __/ |                            
;                                                                          |___/                             
;
;  _              _           
; | |_  ___ _ __ (_)_ _  __ _ 
; | ' \/ _ \ '  \| | ' \/ _` |
; |_||_\___/_|_|_|_|_||_\__, |
;                       |___/ 
;❗️assumes voron tap and sensorless homing and presence of _HOME_X and _HOME_Y macros
;❗️refer to https://docs.vorondesign.com/community/howto/clee/sensorless_xy_homing.html
;
[homing_override]
axes: xyz
gcode:
    ## undock from the purginator (will be skipped if not docked)
    _PURGINATOR_UNDOCK
    ## set variables
    {% set pvars = printer['gcode_macro _PURGINATOR_VARS'] %}
    {% set home_all = 'X' not in params and 'Y' not in params and 'Z' not in params %}  
    ## X homing
    {% if home_all or 'X' in params %}
        ## respond
        {% if params.RESPOND|default(pvars.respond_detail_level)|int >= 1 %}
            RESPOND TYPE=command MSG="🏚️ Homing X axis ..." 
        {% endif %}
        ## home X
        _HOME_X 
    {% endif %}
    ## Y homing
    {% if home_all or 'Y' in params %}
        ## respond
        {% if params.RESPOND|default(pvars.respond_detail_level)|int >= 1 %}
            RESPOND TYPE=command MSG="🏚️ Homing Y axis ..." 
        {% endif %} 
        ## home Y
        _HOME_Y 
    {% endif %}
    ## Z homing
    {% if home_all or 'Z' in params %}
        ## prepare nozzle
        _PURGINATOR_PREPARE_NOZZLE_FOR_PROBING
        ## xy travel to homing position
        _purginator_travel X={pvars.z_homing_pos_x} Y={pvars.z_homing_pos_y}
        ## respond
        {% if params.RESPOND|default(pvars.respond_detail_level)|int >= 1 %}
            RESPOND TYPE=command MSG="🏚️ Homing Z axis ..." 
        {% endif %} 
        ## home Z
        G28 Z
        ## z travel to height after homing
        _purginator_travel Z={pvars.z_height_after_homing}
    {% endif %}
    ## dock to the purginator
    _PURGINATOR_DOCK


;                    _                 _              _             _ _ _           
;  __ _ _  _ __ _ __| |  __ _ __ _ _ _| |_ _ _ _  _  | |_____ _____| | (_)_ _  __ _ 
; / _` | || / _` / _` | / _` / _` | ' \  _| '_| || | | / -_) V / -_) | | | ' \/ _` |
; \__, |\_,_\__,_\__,_| \__, \__,_|_||_\__|_|  \_, | |_\___|\_/\___|_|_|_|_||_\__, |
;    |_|                |___/                  |__/                           |___/ 
;
[gcode_macro QUAD_GANTRY_LEVEL]
rename_existing: _QUAD_GANTRY_LEVEL
gcode:
    ## undock from the purginator
    _PURGINATOR_UNDOCK
    ## Prepare nozzle
    _PURGINATOR_PREPARE_NOZZLE_FOR_PROBING
    ## respond
    {% if params.RESPOND|default(printer['gcode_macro _PURGINATOR_VARS'].respond_detail_level)|int >= 1 %}
         RESPOND TYPE=command MSG="⚖️ Quad Gantry Levelling ..."
    {% endif %}
    ## original QGL
    _QUAD_GANTRY_LEVEL
    ## dock to the purginator
    _PURGINATOR_DOCK




;  _____                 _             _               _    _                 __  __                          
; |  __ \               (_)           | |             | |  | |               |  \/  |                         
; | |__) |   _ _ __ __ _ _ _ __   __ _| |_ ___  _ __  | |  | |___  ___ _ __  | \  / | __ _  ___ _ __ ___  ___ 
; |  ___/ | | | '__/ _` | | '_ \ / _` | __/ _ \| '__| | |  | / __|/ _ \ '__| | |\/| |/ _` |/ __| '__/ _ \/ __|
; | |   | |_| | | | (_| | | | | | (_| | || (_) | |    | |__| \__ \  __/ |    | |  | | (_| | (__| | | (_) \__ \
; |_|    \__,_|_|  \__, |_|_| |_|\__,_|\__\___/|_|     \____/|___/\___|_|    |_|  |_|\__,_|\___|_|  \___/|___/
;                   __/ |                                                                                     
;                  |___/                                                                                      
;
;
; This section contains user macros for the various tasks the purginator can carry out.



[gcode_macro DOCK]
description: Dock the toolhead to the purginator
gcode:
    _purginator_autohome_xy
    _PURGINATOR_DOCK {rawparams}

[gcode_macro UNDOCK]
description: Release the toolhead from the purginator
gcode:
    _PURGINATOR_UNDOCK {rawparams}


[gcode_macro AWAY]
description: Make toolhead and purginator components accessible for manual intervention
gcode:
    _purginator_autohome_xyz
    _PURGINATOR_AWAY


[gcode_macro BRUSH]
description: Brush the nozle
description: Override default wipes and zigzags with parameters WIPE and ZIGZAG
gcode:
    _purginator_autohome_xy
    _PURGINATOR_BRUSH {rawparams}


[gcode_macro CLEAN]
description: Clean the nozzly by heating up and repeatedly brushing it during cooldown
description: 
gcode:
    _purginator_autohome_xy
    _PURGINATOR_CLEAN_NOZZLE


[gcode_macro COOLDOWN]
description: Turn off nozzle heating and repeatedly brush the nozzle until cool.  
description: Makes nozzle cooling twice as fast and nozzle will be clean.
gcode:
    _purginator_autohome_xy
    _PURGINATOR_RAPID_NOZZLE_COOLING {rawparams}


[gcode_macro PURGE]
description: Purge Filament according to settings
gcode:
    _purginator_set_minimum_nozzle_temp
    _purginator_autohome_xyz
    _PURGINATOR_PURGE {rawparams}
    _purginator_set_original_nozzle_temp


[gcode_macro CUT]
description: Cut Filament Tip for filament change
gcode:
    _purginator_autohome_xy
    _purginator_set_minimum_nozzle_temp
    _PURGINATOR_CUT
    _purginator_set_original_nozzle_temp

    
[gcode_macro FLUSH]
description: Empty the purge tray 
gcode:
    _EXTRACTOR_EMPTY_TRAY {rawparams}
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

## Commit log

2024-06-02 Create bom
2024-09-10 Update purginator_vars.cfg
    added prime tower volume reduction function for purge volume calculation
    [purginator_vars.cfg]
2024-09-10 Update purginator.cfg
    Added option for reducing calculated purge volume by prime tower purge volume if prime tower is enabled in orca slicer
    [purginator.cfg]
2024-09-17 Update purginator.cfg
    return sequence modified so that initial tool change is not different from subsequent tool changes and toolhead placed at print start position.
    [purginator.cfg]
2024-09-22 Update purginator.cfg
    Added G4 commands to stop the nozzle cooling macro and homing override to cause mcu timer too close errors which occurred since last Klipper update.
    [purginator.cfg]
2024-09-22 Update purginator.cfg
    changed _PURGINATOR_HAPPY_POST_LOAD extension so that no gantry movement or retraction will take place when not printing
    [purginator.cfg]
2024-10-24 Update purginator.cfg
    modified nozzle wipe
    [purginator.cfg]
2024-11-11 Update purginator.cfg
    fixed _purginator_wait
    [purginator.cfg]
